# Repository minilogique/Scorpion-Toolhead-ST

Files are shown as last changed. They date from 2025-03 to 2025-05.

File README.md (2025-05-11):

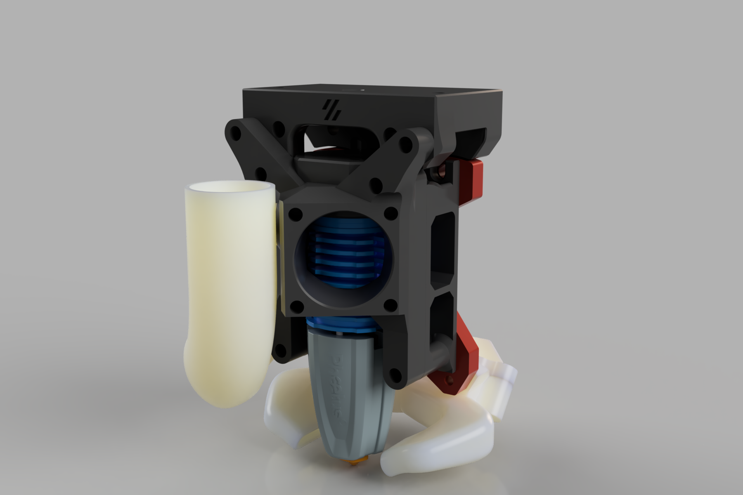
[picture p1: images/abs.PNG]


I wanted a toolhead for CNC TAPv2 that also supports big hotend, has CPAP cooling and has clear access and visibility to the nozzle and hotend for maintenance. It uses the same Stealthburner carriage pattern so if it holds the classic Stealthburner, this here also fits.

Let's start from the top - extruder carrier. Cutdown version of the original carrier from CrownCooler toolhead and possibly even the original Stealthburner extruder mount. I have not tested the fitment, but it might work. Added access holes for 3mm hex tool for easier access, strengthened frame around heat insert. Uses same hardware as official Stealthburner part.

The length of the microbowden for Rapido version is 27.5mm and for Goliath version it's 20.5mm.

Hotend carriage - originally with 4010 axial fan on CrownCooler toolhead and fairly chonky look with added duct for part-cooling-cooling so it would not melt. I did not have any luck with 4010 as the backpressure caused by the heatbreak ducting hindered the fan almost useless with PETG prints with closed enclosure. So, enter high-performance SUNON 2510 axial fan and heatbreak ducting with perfect ducting. Uncut Peopoly Lancer Long hotend at 220C took the heatbreak radiator with freshly added thermal paste just below 40C and hotend at 300C the heatbreak barely got over 51C. Measured with a bit more expensive multimeter with thermal probe up to 1000C. Installs with same hardware as Stealthburner for the main mounting points, additionally three 5mm M3 heat inserts that might need some filing in the radiator tunnel.

Part-cooling - original ducts that are available for CrownCooler cool great, look decent but do not work with CNC TAP carriage as the lower portions on the toolhead plate obstruct the space the ducts use. At first I tinkered around with asymmetrical front-mounted ducts that were single piece the part-cooling power was sub-par. Lurking around in other printers communities I stubled upon a dual-duct design for VzBot printers by VITALS. I got the thumbs-up for adapting it to my toolhead and after about a month or so I have the properly working and rigid part-cooling system. Uses two M3x6mm flathead bolts to mount the ducts to the lowest M3 holes on CNC TAP toolhead carrier and after that you install the manifold with two M3x12 regular hexheads to the duct and one M3x8 hexhead to the front top side to secure the manifold and note that - CPAP hose does not need a cable tie as if you pull the hose on the manifold and then tighten up the M3 bolt, it will squeeze the hose between the manifold and toolhead itself. Greatly benefits from having the CPAP hose tied to the umbilical/PTFE tube.

ATTENTION - the ducts themselves should be printed with something more heat-resistant if you plan to print with plate above 100C as these ducts will get soft and sag causing collision with the prints. So in that case use at least ASA-CF or something more baller like nylons or polycarbonate etc.

Models are not placed as how to print them. In my experience Orca slicer has automatically managed to choose the best orientation for these parts and it is higly recommended to tune in your supports for these prints as at least front piece and the manifold will need the supports so it might never get an official Voron Mod status, but it's an awesome toolhead nevertheless in my opinion.

Beta phase is over. Renamed the toolhead from ScorpionCooler to Scorpion Toolhead or ST for short and added a quick iteration of hevORT toolhead's TentaCool part cooling duct as a secondary option (this is as of today, untested, but the VITALS' duct is proven). Did some minor fixes here and there.

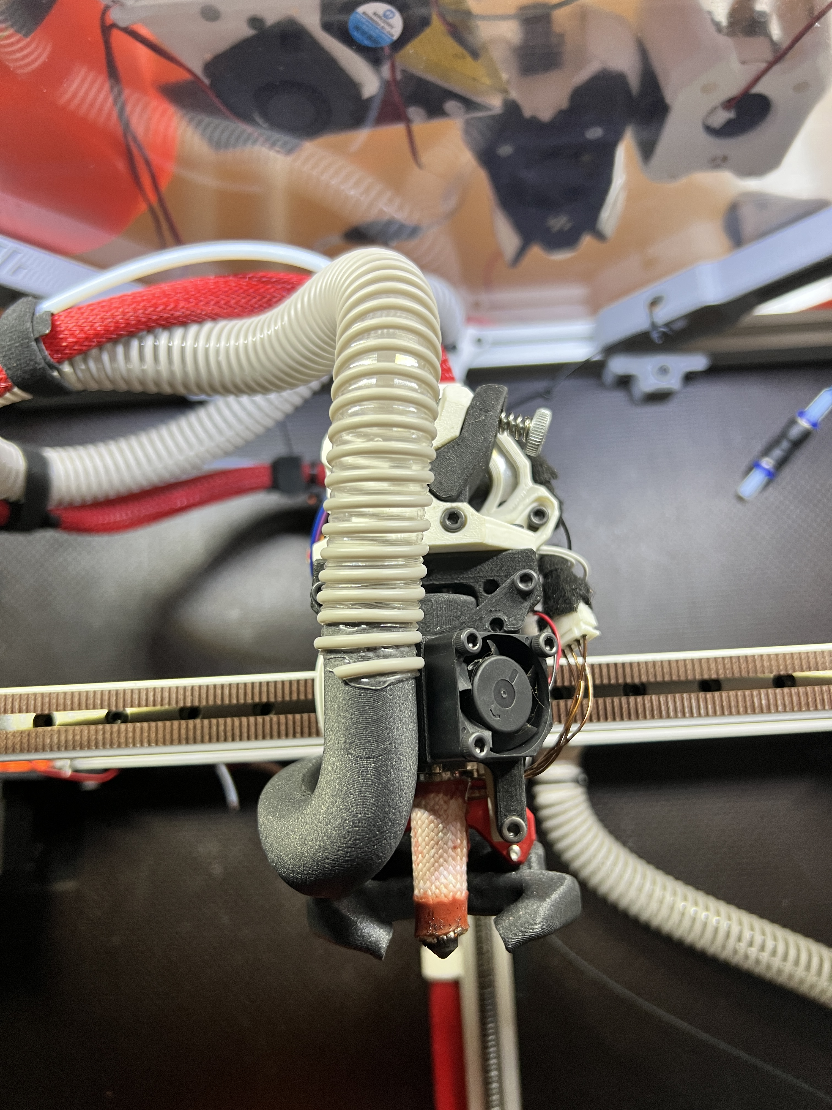
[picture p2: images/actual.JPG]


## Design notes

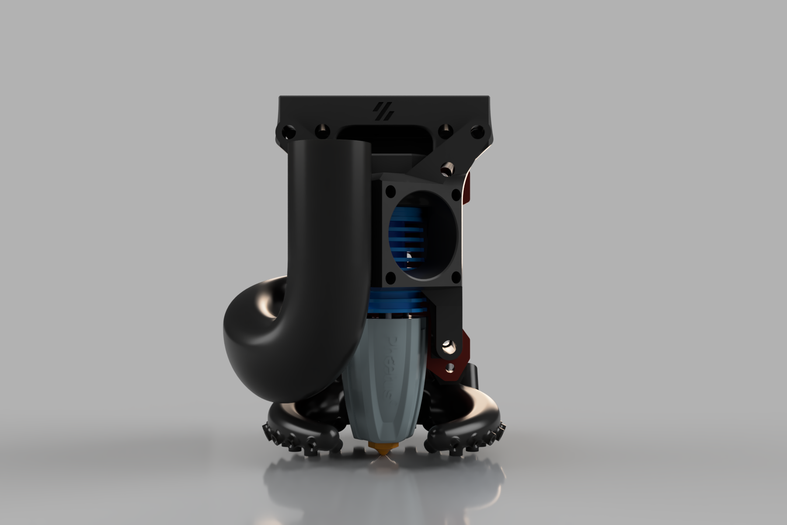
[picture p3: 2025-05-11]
images/rapidouhf tenta.png

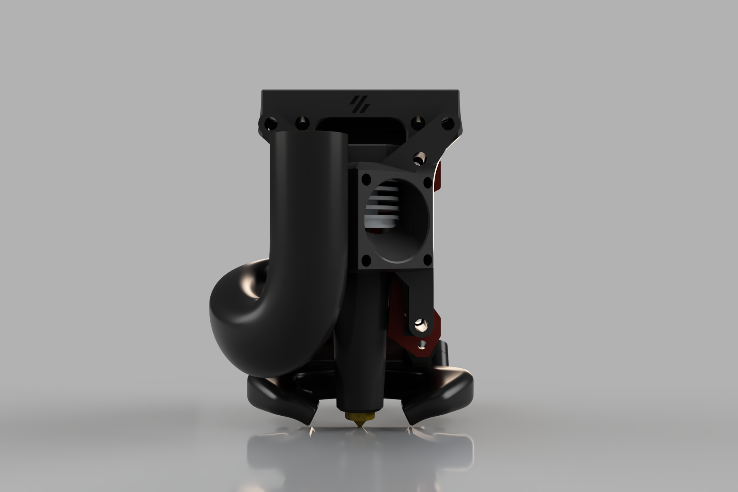
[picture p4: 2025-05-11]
images/goliath vitals.png

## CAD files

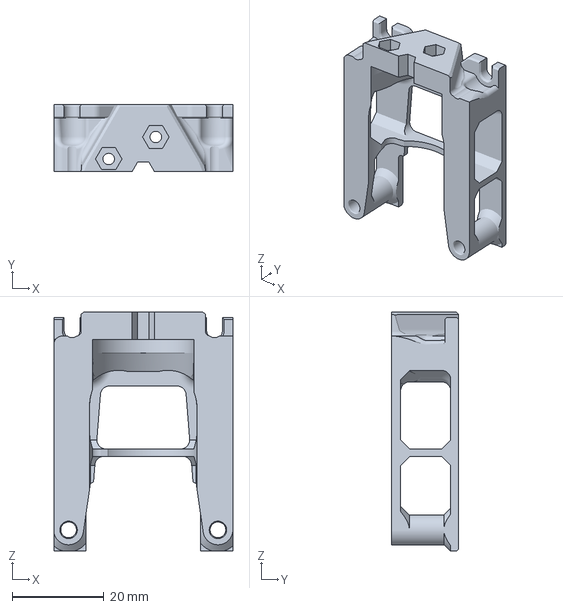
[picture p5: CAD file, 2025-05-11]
3mf/Goliath rear v2 for ST.3mf
38.9 x 14.6 x 52.0 mm

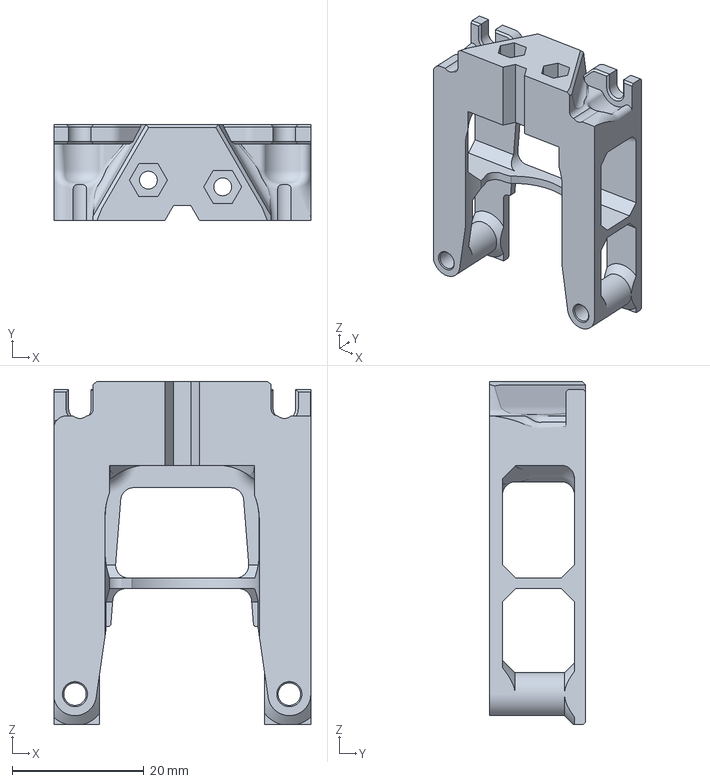
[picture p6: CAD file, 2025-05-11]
3mf/Rapido UHF rear v2 for ST.3mf
38.9 x 14.6 x 52.0 mm

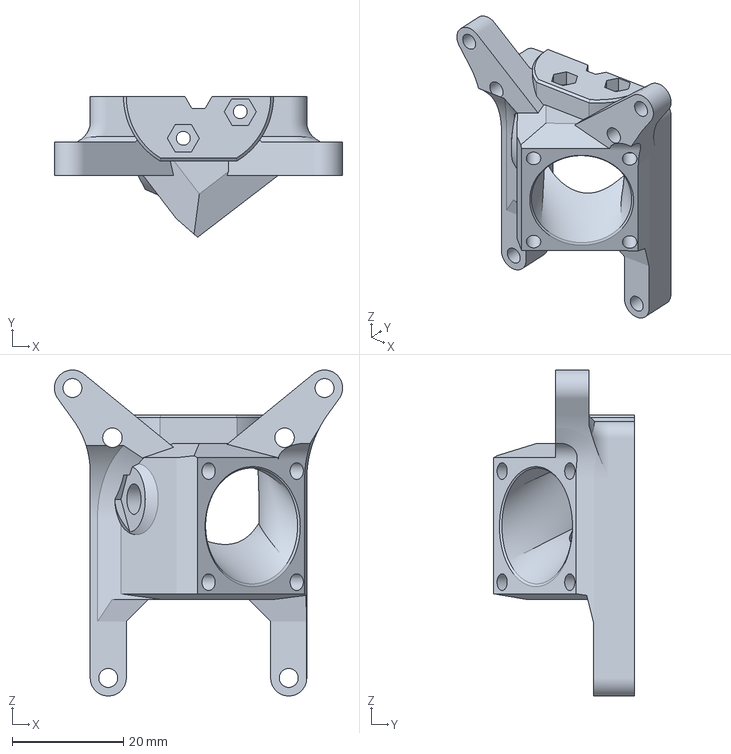
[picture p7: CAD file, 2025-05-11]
3mf/Goliath front v2 for ST.3mf
51.9 x 25.3 x 58.7 mm

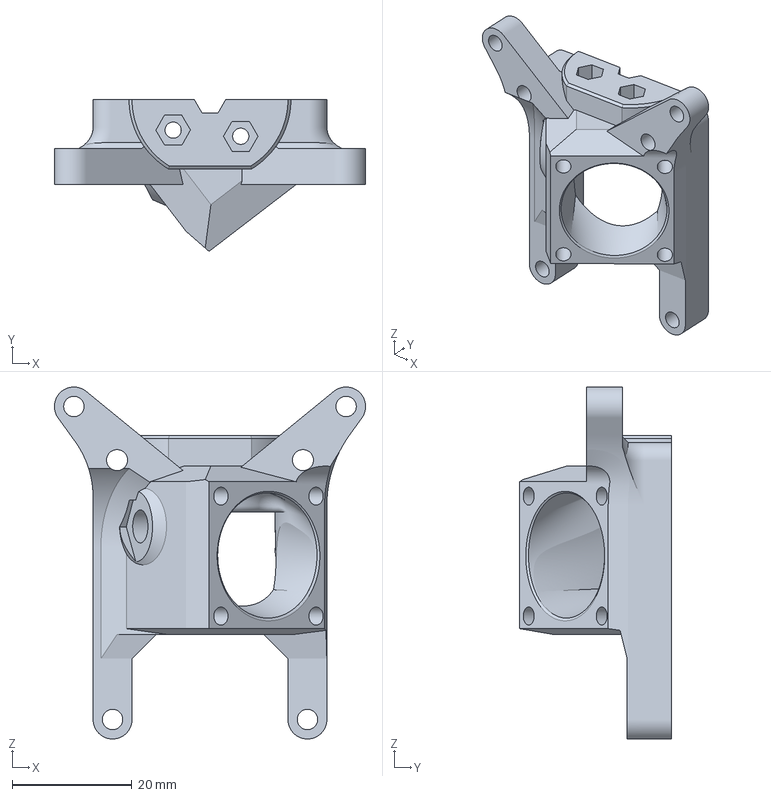
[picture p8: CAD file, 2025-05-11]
3mf/Rapido UHF front for ST.3mf
51.9 x 25.3 x 58.7 mm

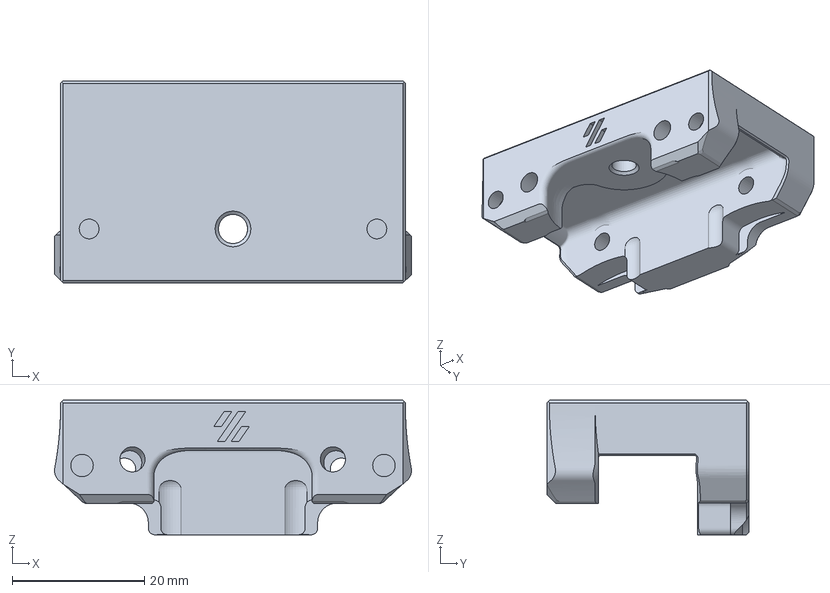
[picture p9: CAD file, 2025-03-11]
3mf/sherpa mini mount for SB.3mf
54.0 x 30.6 x 20.4 mm

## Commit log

2025-03-11 removed files I don't use or see fit with my design
    [2510 Goliath CrownCooler front.3mf, 2510 Goliath CrownCooler rear.3mf, 4028FanCPAPDuct.stl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]
2025-03-11 Create Scorpion Toolhead manifold and ducts.step
2025-05-11 update
    minor adjustments to part-cooling parts; major - added Rapido UHF support; new renders; updated text
    [Goliath front for ST.3mf, Goliath rear for ST.3mf, Rapido UHF front for ST.3mf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]
2025-05-11 some fixes
    [Goliath front for ST.3mf, Goliath front v2 for ST.3mf, Goliath rear for ST.3mf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]
